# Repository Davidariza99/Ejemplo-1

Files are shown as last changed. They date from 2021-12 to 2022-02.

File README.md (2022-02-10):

# Proyecto embebidos (Pet_Sitting)

## Integrantes:

- David Ariza
- Andres Unibio
- Sharem Alonso

## Descripción:
Vigilante y cuidador de mascotas en casa, permite al usuario interactuar con su mascota a la distacia.

## Justificación: 
Se ha presentado un aumento significativo de la adopción de mascotas durante la pandemia, a medida que las personas vuelven a sus oficinas, universidades y demas obligaciones fuera del hogar, las mascotas que fueron criadas con la constante compañia de sus dueños, ahora sienten su ausencia. Este proyecto busca crear un nuevo vinculo entre el dueño y la mascota mientras este no se encuentre en casa

## Requerimientos funcionales:
- Vigilar 
- Comando de voz: Llamar, consentir, felicitar y corregir
- Movilidad (en un solo nivel)

## Requerimientos no funcionales:
- Cámara
- Audios pregrabados (mp3)
- Motor y alimentación
- Módulo WiFi
- Control remoto (desde un dispositivo móvil)

## Diagrama de bloques:
### Propuesto
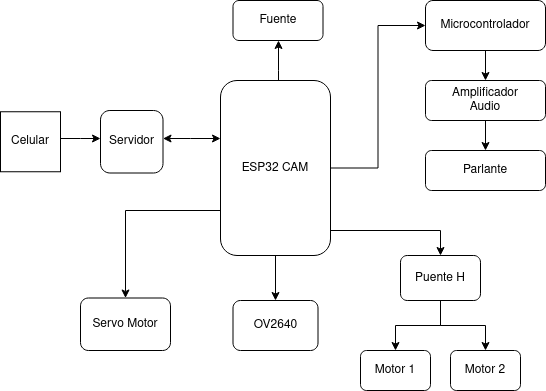
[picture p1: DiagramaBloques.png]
Diagrama_bloques drawio

### Final
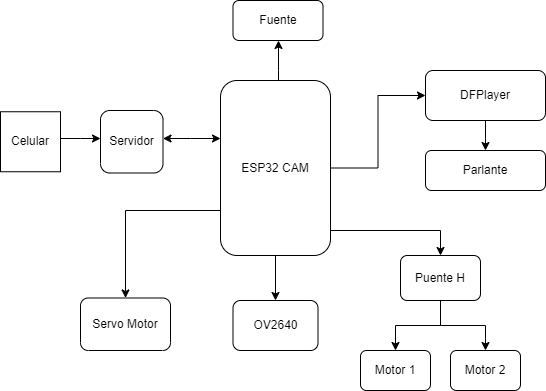
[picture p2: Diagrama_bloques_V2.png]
Diagrama_bloques drawio


## Proceso:
Ya teniendo definida la idea del proyecto, se procede a escoger cada uno de los elementos que nos permitirán realizar las tareas requeridas. Se pensó inicialmente en usar como módulo principal el ESP32, sin embargo, teniendo en cuenta el requerimiento de la cámara y que las referencias de cámara consultadas para usar en el ESP32 como la OV7670 tienen cierta complejidad al momento de configurarla y no ofrecen la mejor calidad, se decidió buscar otro módulo que contará con mejores especificaciones y facilitará el proceso. La ESP32 CAM cuenta con una cámara OV2460, que ofrece una mejor calidad y ya viene configurada a la placa.

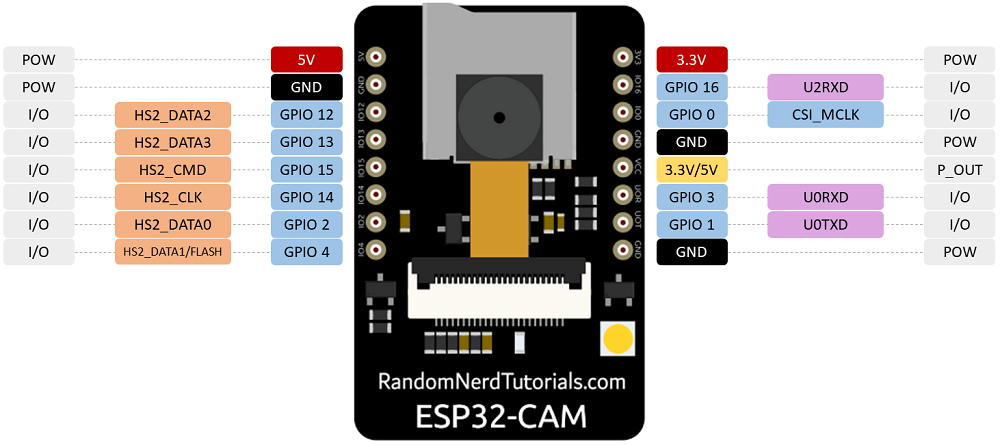
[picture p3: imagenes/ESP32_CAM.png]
ESP32_CAM


Teniendo claro esto, lo siguiente era el desplazamiento ¿Cómo hace que esta ESP32 CAM se desplaze por el espacio para cumplir la labor de vigilancia? Se escogió un puente H (L293D) conectados a dos motores que le darán esa habilidad, además de montar la tarjeta en un servo motor para tener la capacidad también de mover la cámara. 

Ya cumpliendo con los primeros requerimiento de cámara y desplazamiento, el siguiente es el de la intereacción que se tendrá con la mascota. Para esto, la interacción mas viable es la de poder hablar con ellos, con nuestra propia voz, debido a esto se tuvieron variass opciones. Teniendo en cuenta las limitaciones de pines del ESP32 CAM no era posible conectar el amplificador y parlante para emitir los audios pregrabados, por lo que se optó por la opción de un esclavo.

La primera opción, que se puede observar en el primer diagrama de bloques propuesto, tenía como esclavo un microcontrolador con el DAC integrado, necesario para enviar las señales a un amplificador y después al parlante. Sin embargo, el chip del microcontrolador escogido ocupaba mucho espacio para las pocas conexiones que se pensaban hacer, además tampoco se contó con suficiento documentación para su funcionamiento.

Debido a lo anterior, se optó por el DFPlayer Mini un modulo reproductor de audio mp3 con amplificador integrado y que incluso puede funcionar por si solo simplemente conectando pulsadores. Por lo que se acomodaba muy bien a nuestras necesidades.

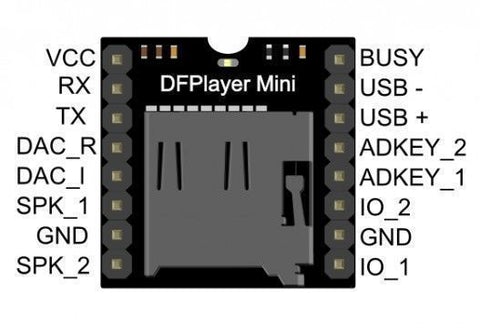
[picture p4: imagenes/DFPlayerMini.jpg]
DFPlayer mini


De esta manera se obtuvo el diagrama de bloques final, donde hay adicional un bloque nombrado "servidor" que es una configuración que se establece por software para poder controlar nuestro dispositivo de manera remota.

## Esquemático

El siquiente esquemático fue el realizado para la implementación, teniendo en cuenta las recomendaciones de conexión de por ejemplo el DFPlayer mini, que para recepción y emisión se agregaron unas resistencias en serie para eliminar el ruido. Para la entrada se agregó un regulador de tensión para asegurar a la salida una tensión de 5V que es lo necesario para alimentar nuestro circuito.

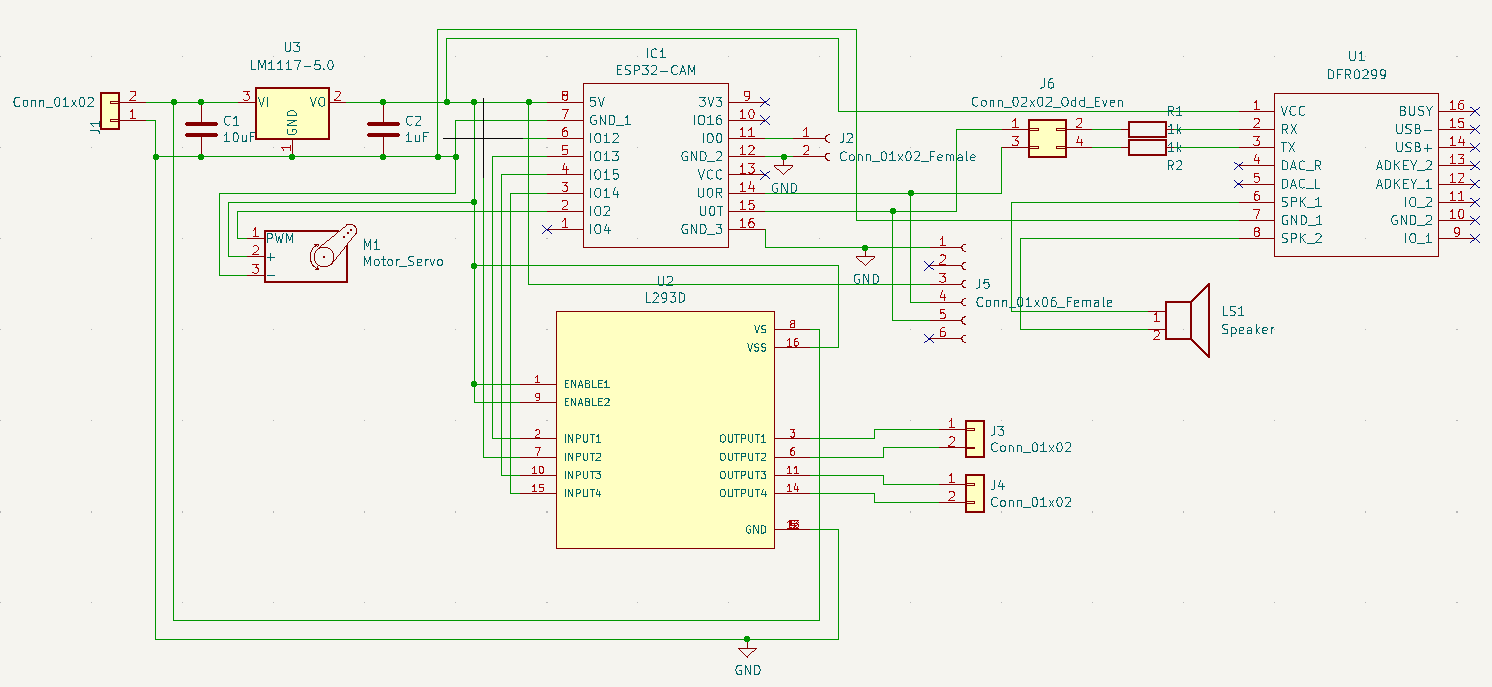
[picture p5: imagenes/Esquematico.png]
Esquemático


## PCB

La primera versión de la PCB se realizó sin tener en cuenta anchos de los caminos, lo cual es importante ya que si son muy delgados no funcionará correctamente el circuito, se necesitan caminos mas anchos para la transmisión de potencia y de información. También se puede observar que no se hizo uso de las vías en más capas, creando muchos caminos en formas no convenientes que pueden generar inductancias indeseadas.

### Versión 1

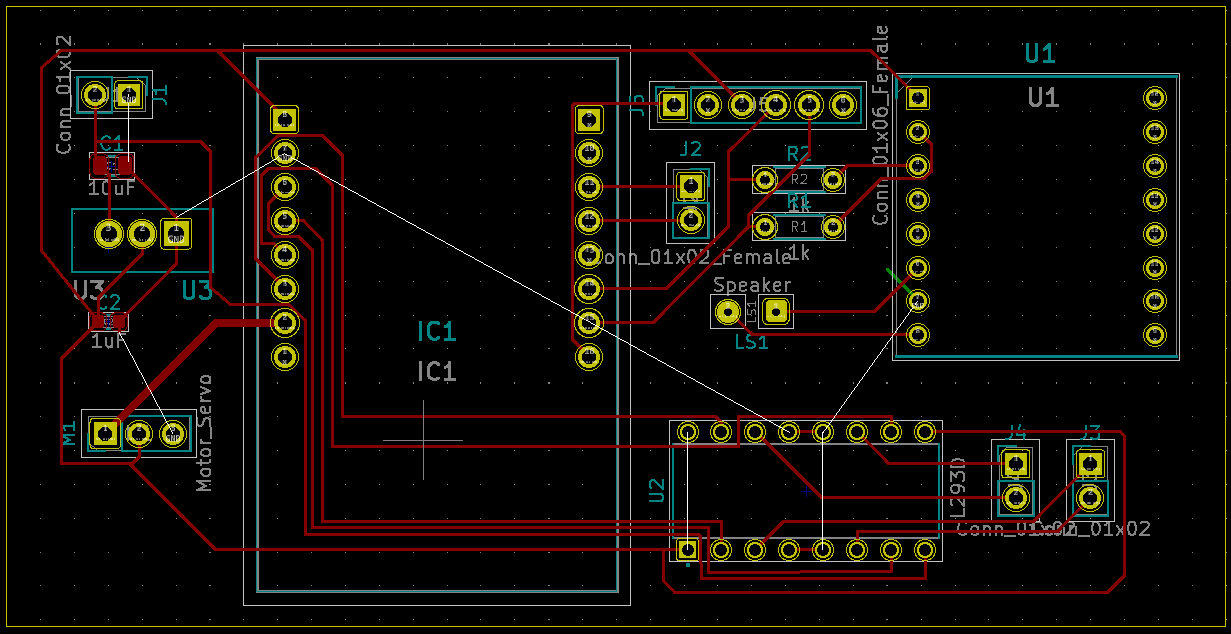
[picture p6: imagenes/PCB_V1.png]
PCB V1


### Versión final

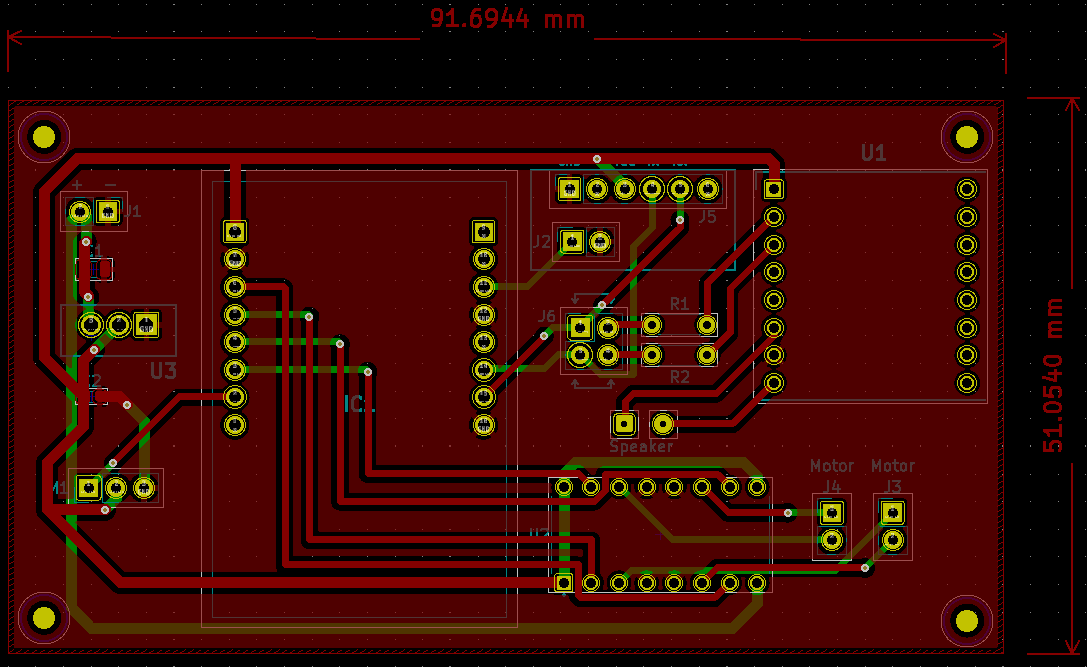
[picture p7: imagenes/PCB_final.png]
PCB final


## Programación

Para realizar la programación de nuestro pet sitting, se hizo uso de la plataforma de arduino. Se hizo la siguiente conexión para poder programar nuestra ESP32 CAM:

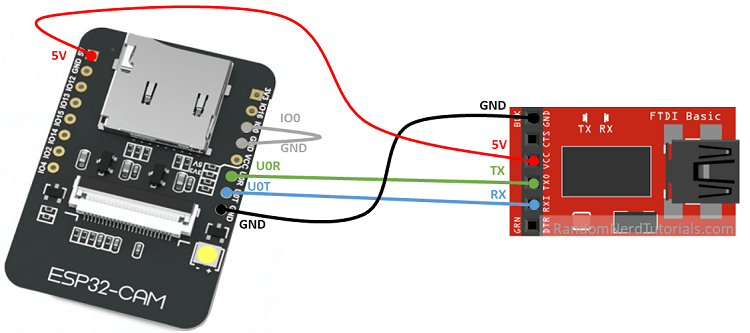
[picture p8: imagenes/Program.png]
Programming


de esta manera y descargando las librerías adecuadas, se puede acceder a un ejemplo de CameraWebServer, donde podemos observar el funcionamiento de la cámara, conenctándose remotamente desde un teléfono celular a una IP generada por el ESP32 CAM

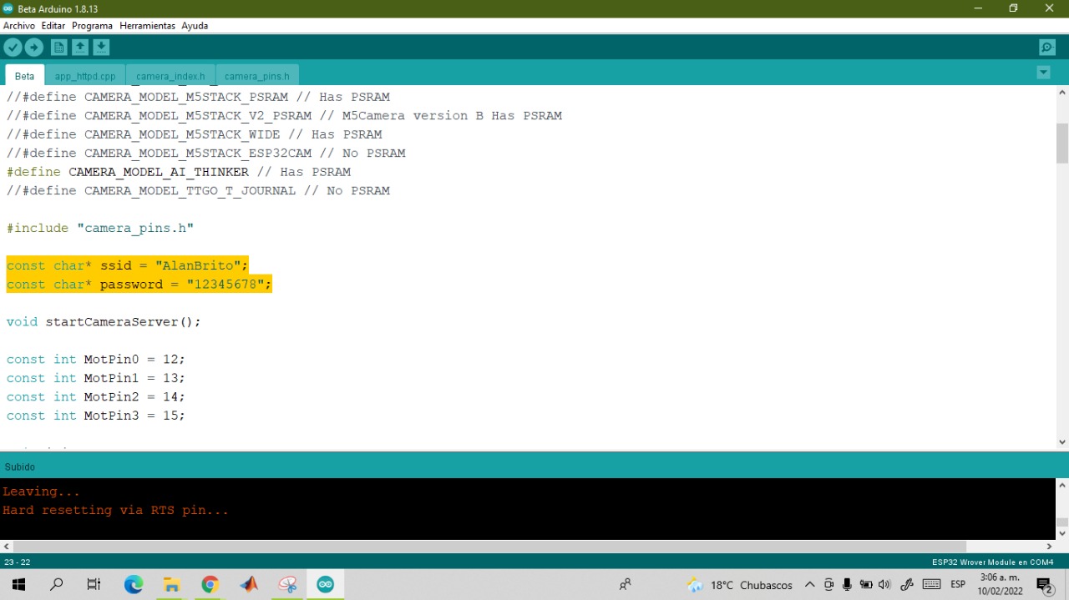
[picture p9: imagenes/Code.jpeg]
Code


Para luego hace las adiciones en el código de nuestros motores y el servomotor, teniendo nuestro programa listo para ser ejecutado por nuestra placa

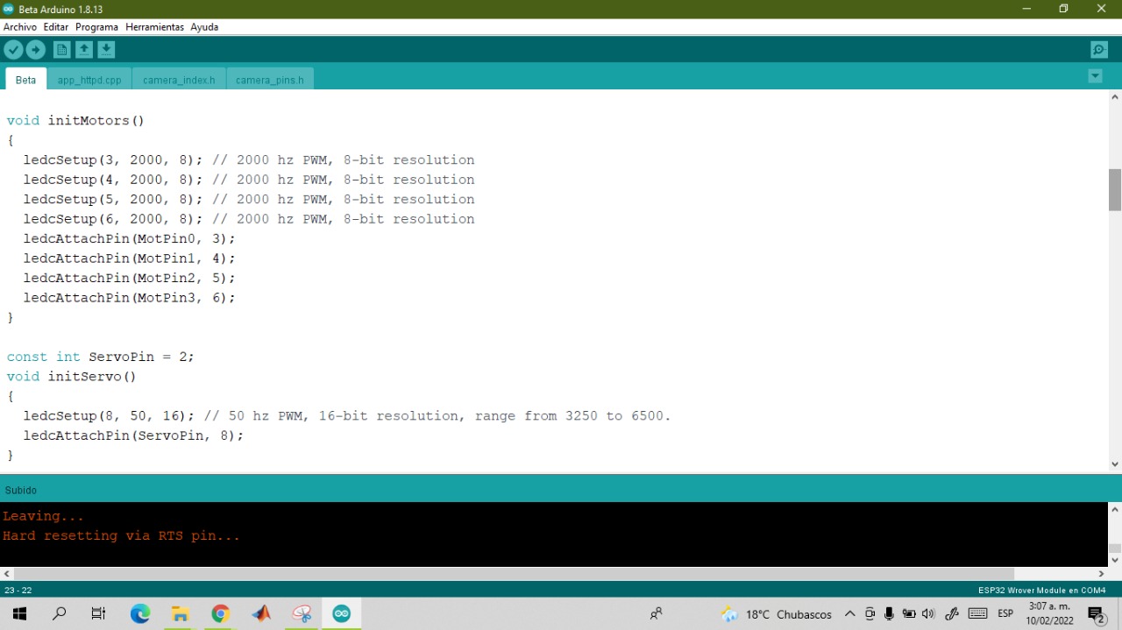
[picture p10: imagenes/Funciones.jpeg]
Funciones


El ejemplo además contaba con una interfaz gráfica que podíamos observar al momento de conectarnos a la IP, interfaz que se vió modificada, teniendo en cuenta nuestros requerimientos, agragando botones para el movimiento de motores y servo, además de deslizadores para controlar características de la cámara

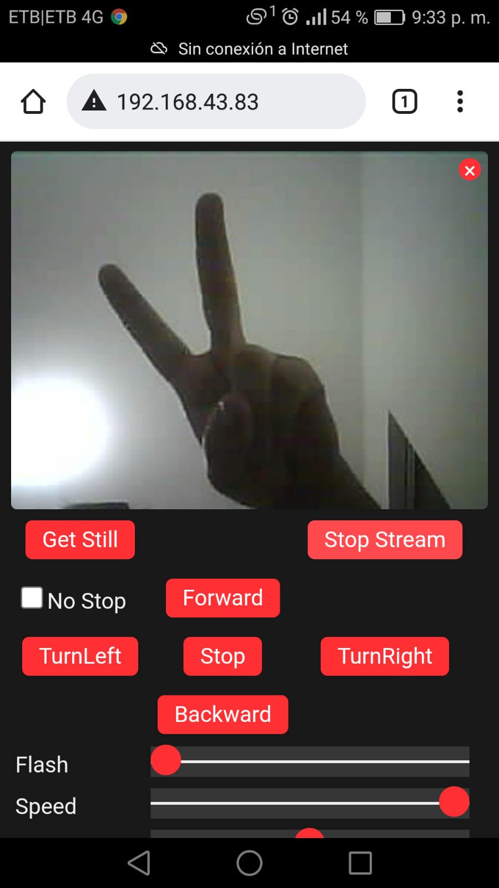
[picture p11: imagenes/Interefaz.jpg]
Interfaz


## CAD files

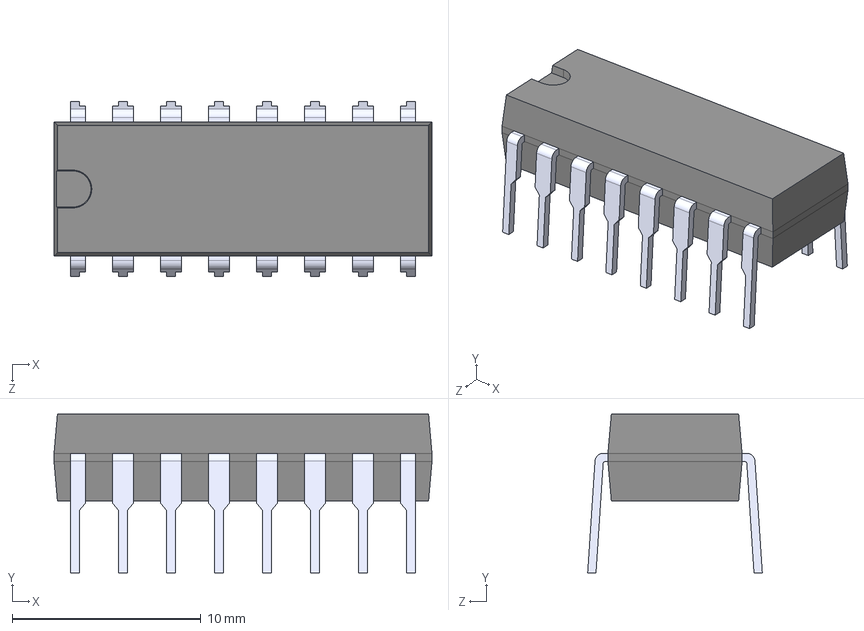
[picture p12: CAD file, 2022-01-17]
PCB/Librerias/L293D/L293D.step
20.0 x 8.40 x 9.24 mm

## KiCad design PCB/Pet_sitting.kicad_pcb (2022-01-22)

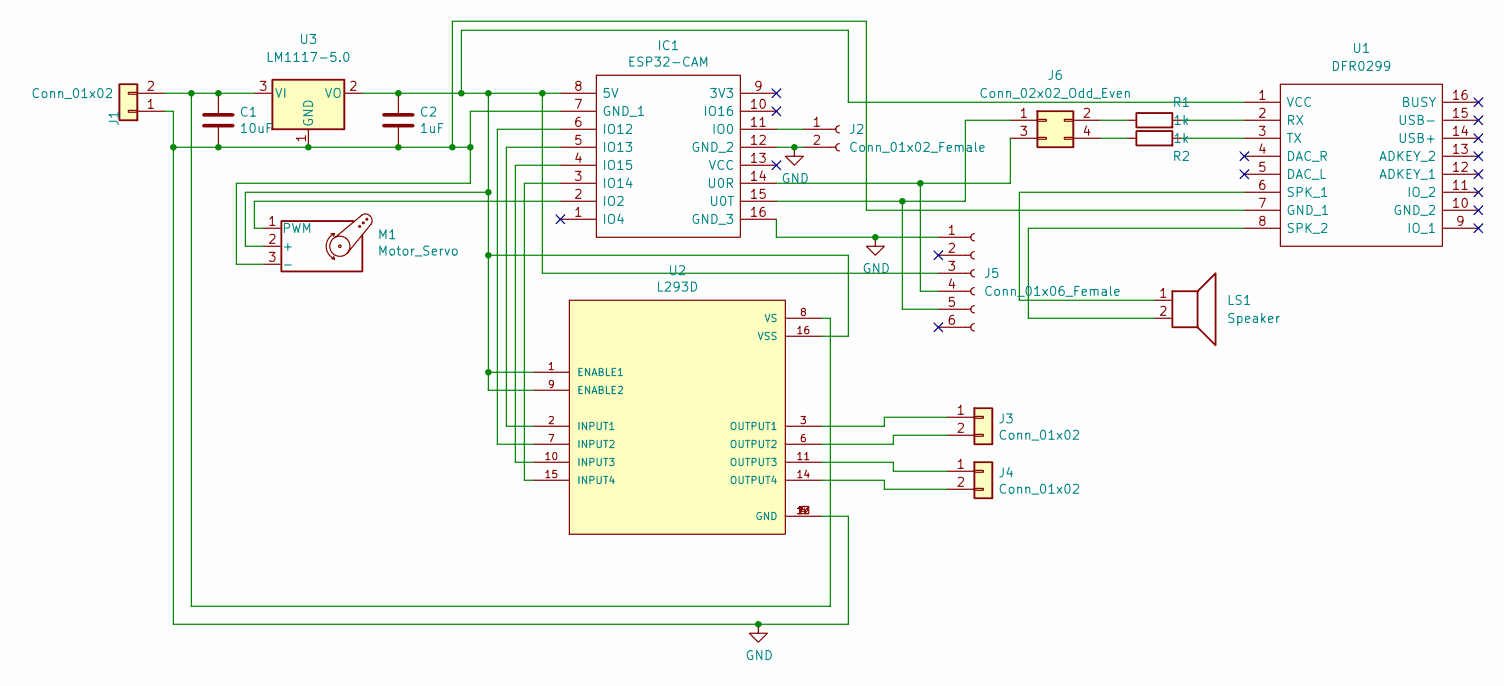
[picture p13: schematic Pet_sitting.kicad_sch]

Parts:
C1: 10uF; C_0805_2012Metric
C2: 1uF; C_0603_1608Metric
IC1: ESP32-CAM; ESP32CAM; Manufacturer_Part_Number ESP32-CAM
J1, J3, J4: Conn_01x02; PinHeader_1x02_P2.54mm_Vertical
J2: Conn_01x02_Female; PinSocket_1x02_P2.54mm_Vertical
J5: Conn_01x06_Female; PinSocket_1x06_P2.54mm_Vertical
J6: Conn_02x02_Odd_Even; PinHeader_2x02_P2.54mm_Vertical
LS1: Speaker; SolderWire-0.1sqmm_1x02_P3.6mm_D0.4mm_OD1mm
M1: Motor_Servo; PinHeader_1x03_P2.54mm_Vertical
R1, R2: 1k; R_Axial_DIN0204_L3.6mm_D1.6mm_P5.08mm_Horizontal
U1: DFR0299; DIPS1778W50P254L2100H170Q16N; Manufacturer_Part_Number DFR0299; Mouser Part Number 426-DFR0299
U2: L293D; DIP880W50P254L2000H510Q16
U3: LM1117-5.0; TO254P470X1016X2222-3P

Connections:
GND: C1.2, C2.2, IC1.7 (GND_1), IC1.12 (GND_2), IC1.16 (GND_3), J1.1, J2.2, J5.1, M1.3 (-), U1.7 (GND_1), U2.4 (GND), U2.5 (GND), U2.12 (GND), U2.13 (GND), U3.1 (GND)
unnamed: C1.1, J1.2, U2.8 (VS), U3.3 (VI)
unnamed: C2.1, IC1.8 (5V), J5.3, M1.2 (+), U1.1 (VCC), U2.1 (ENABLE1), U2.9 (ENABLE2), U2.16 (VSS), U3.2 (VO)
unnamed: IC1.2 (IO2), M1.1 (PWM)
unnamed: IC1.3 (IO14), U2.15 (INPUT4)
unnamed: IC1.4 (IO15), U2.10 (INPUT3)
unnamed: IC1.5 (IO13), U2.2 (INPUT1)
unnamed: IC1.6 (IO12), U2.7 (INPUT2)
unnamed: IC1.11 (IO0), J2.1
unnamed: IC1.14 (U0R), J5.4, J6.3
unnamed: IC1.15 (U0T), J5.5, J6.1
unnamed: J3.1, U2.3 (OUTPUT1)
unnamed: J3.2, U2.6 (OUTPUT2)
unnamed: J4.1, U2.11 (OUTPUT3)
unnamed: J4.2, U2.14 (OUTPUT4)
unnamed 15: LS1.1, U1.6 (SPK_1); also elsewhere on the board
unnamed 16: LS1.2, U1.8 (SPK_2); also elsewhere on the board
unnamed: J6.2, R1.1
unnamed: J6.4, R2.1
unnamed: R1.2, U1.2 (RX)
unnamed: R2.2, U1.3 (TX)

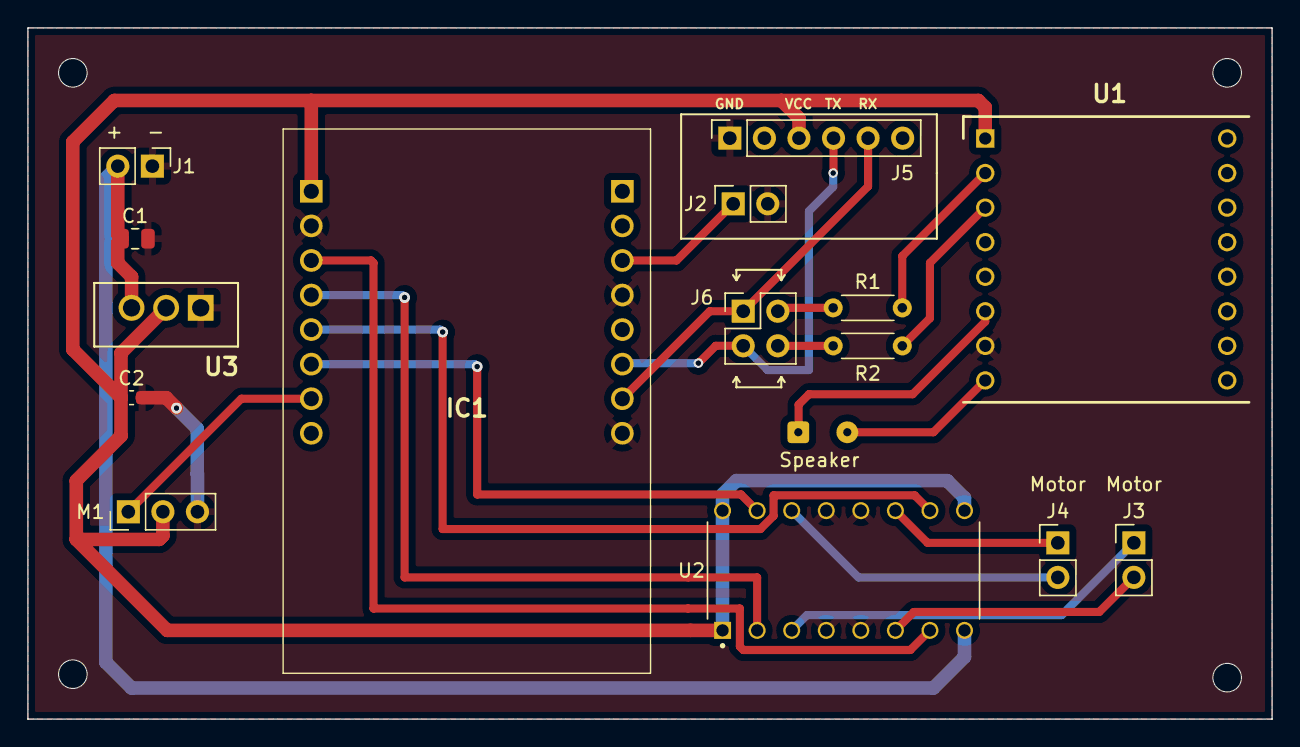
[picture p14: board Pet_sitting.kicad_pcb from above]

Board: 2 copper layers, 91.4 x 50.8 mm, 16 parts (0 on the bottom side), 21 nets.

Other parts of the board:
Speaker: Speaker; SolderWire-0.1sqmm_1x02_P3.6mm_D0.4mm_OD1mm

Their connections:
unnamed 15: Speaker.1; also elsewhere on the board
unnamed 16: Speaker.2; also elsewhere on the board
